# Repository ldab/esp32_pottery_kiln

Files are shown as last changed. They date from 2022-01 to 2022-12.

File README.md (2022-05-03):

# kiln_controller
Connected electric kiln controller -> esp32, max31855, thermocouple type K, relay, contactor and energy meter. Including Kiln built plans.







 ## TODO

- [ ] Temperature Ramp rate monitor;
- [ ] Cooling monitor;
- [ ] Cool upload progress: https://codepen.io/takaneichinose/pen/jOWXBBd

## VOID

"Lorem ipsum dolor sit amet, consectetur adipiscing elit, sed do eiusmod tempor incididunt ut labore et dolore magna aliqua. Ut enim ad minim veniam, quis nostrud exercitation ullamco laboris nisi ut aliquip ex ea commodo consequat. Duis aute irure dolor in reprehenderit in voluptate velit esse cillum dolore eu fugiat nulla pariatur. Excepteur sint occaecat cupidatat non proident, sunt in culpa qui officia deserunt mollit anim id est laborum."

## Bil of materials

Description | Price
------------ | -------------
[4x Modules enclosure](https://www.amazon.de/gp/product/B07K5X5KZQ/ref=ppx_yo_dt_b_asin_title_o00_s00?ie=UTF8&psc=1) | €8.00
[Energy meter with S0 output](https://www.amazon.de/gp/product/B083H7NT2R/ref=ppx_yo_dt_b_asin_title_o00_s01?ie=UTF8&psc=1) | €13.00
[HDR-15 Power Supply](https://www.amazon.de/gp/product/B06XWQSJGW/ref=ppx_yo_dt_b_asin_title_o00_s00?ie=UTF8&psc=1) | €13.00
[12v/16A Relay](https://www.tme.eu/se/en/details/pi85012dc00ld/electromagnetic-relays-sets/relpol/pi85-012dc-00ld/) | €13.00
esp32 | €5.00
max31855 | €10.00
[Type-K thermocouple](https://www.keramik-kraft.com/en/Kiln-Building--Repair/Pyrometry/Thermocouple-Nickel-Typ-K/Thermocouple-Type-K-open-with-flange-l-12cm.html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) | €50.00
Cables, terminals, etc | €10.00

Total: **€120.00**

## Element calculations

### Element power

* This is determined by the power outlet, i.e `230Vac@16A` -> **3680W**

* Some [resources](https://knifedogs.com/threads/heat-treat-oven-how-to-design-and-calculate-the-heating-elements.21072/) indicate 0.6 - 1.3 W/cm2 of wall -> `Aw = (30.4 * 30.4 * 2) + (30.4 * 34.2 * 4) = 6,007.04 cm2` therefore Element should be between *3604W* and *7800W*.

* [KMT-614](https://skutt.com/products-page/ceramic-kilns/kmt-614/) and [Ecotop 20](https://www.rohde.eu/en/arts-and-crafts/products/toploaders/ecotop-series/ecotop-20) are both ~20L with 2300W element and rated to [Cone 6](https://www.ortonceramic.com/files/2676/File/orton-cone-chart-2016.pdf), aka ~1260°C

### Element size

Using Kanthal D - Other variants were hard to find, Kanthal D can be bought at [eveks.se](https://eveks.se/kategorier/461-kanthal-tr%C3%A5d-01-5mm-v%C3%A4rmekabel-14765-kanthal-d-motst%C3%A5ndstr%C3%A5d-1-100-meter-4066435006815.html)

* 1.6mm -> R = 0.67 Ohms/m
* L = ( 3680 / 16^2 ) / 0.67 = **~21.5m**

### Surface Load

* Accordingly to Kanthal [datasheet](./extras/Kanthal%20handbook.pdf), kiln application should have a Surface Load between 3-9 W/cm2:

`3680 / (2pi x 0.08 x 2150) = **3.4**W/cm2`

* [furnace handbook](./extras/file1359965681_U3423.pdf) page 7 indicates max 2.4W/cm2 @ 1100°C

### Coil Diameter

* In order to avoid deformation on horizontal coils, the coild diameter should stay below 10mm accordingly to:

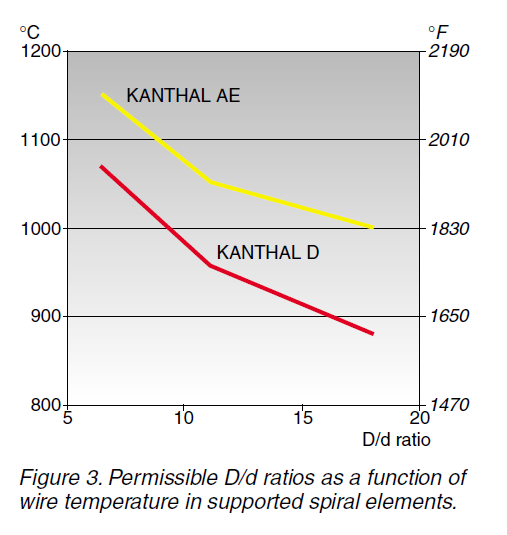
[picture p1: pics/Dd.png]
 

* Therefore let's use a **M8** rod to coil the wire.

### Coil Length

* The internal element perimeter is ~1216mm, if 3x turns are planned, we end up with a **3648mm** coil;

### Coil Pitch

*Coil pitch is normally 2-4 times the wire diameter* [page_79](./extras/Kanthal20handbook.pdf) -> aka 2-4mm

`s = (11.2 - 8) x pi / sqrt((21500 / 3648) ^ 2 - 1) = ~**2mm**`

## Bricks

The kils was build with [JM23](https://www.morganthermalceramics.com/media/4120/ifb-insulation-range-1100-1315-english.pdf) bricks

### Bricks thermal heat loss

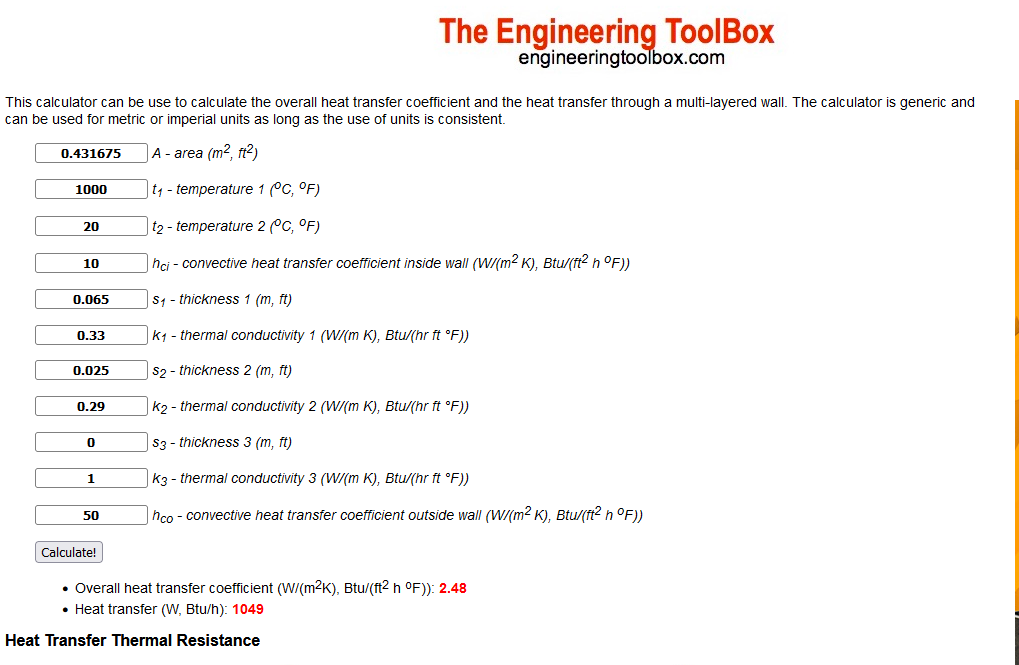
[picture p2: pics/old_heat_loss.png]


## PCB

PCB layout and files are found at [](./pcb/) open it with KiCad

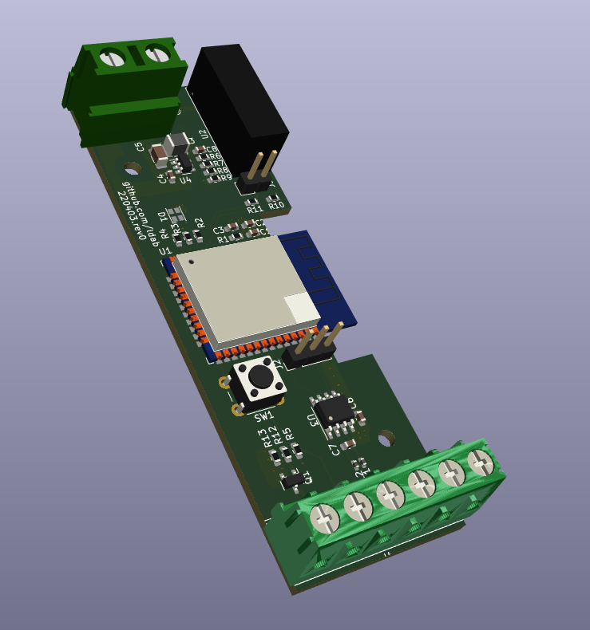
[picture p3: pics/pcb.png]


## Known Limitations

* 

## Credits

Github Shields and Badges created with [Shields.io](https://github.com/badges/shields/)

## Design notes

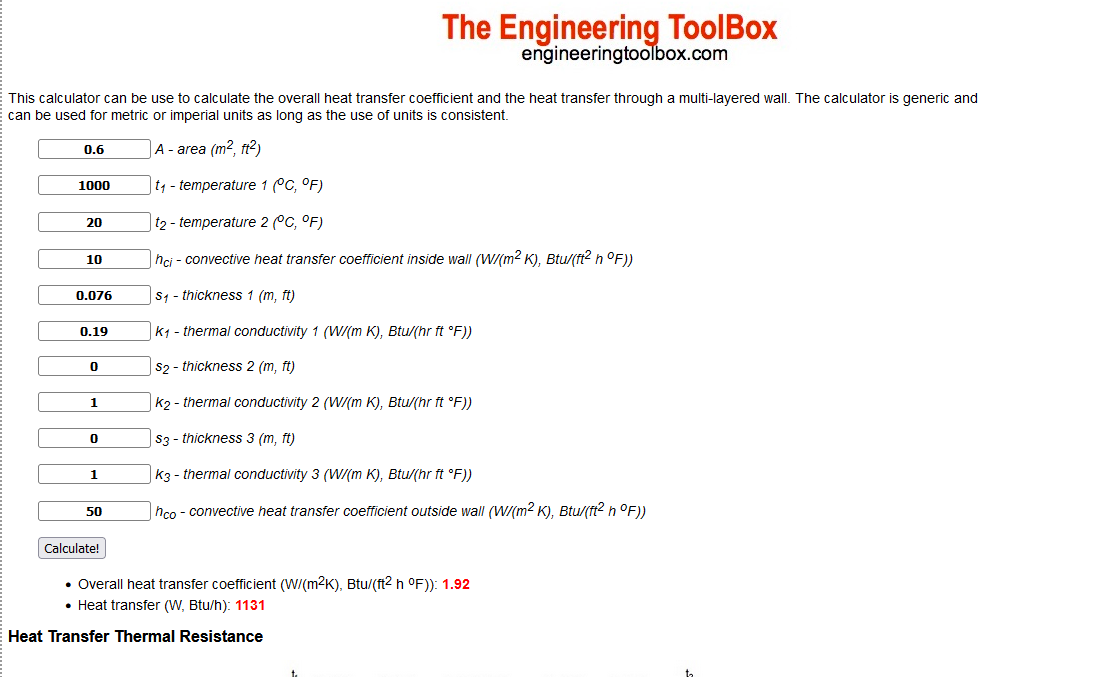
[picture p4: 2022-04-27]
pics/new_heat_loss.png

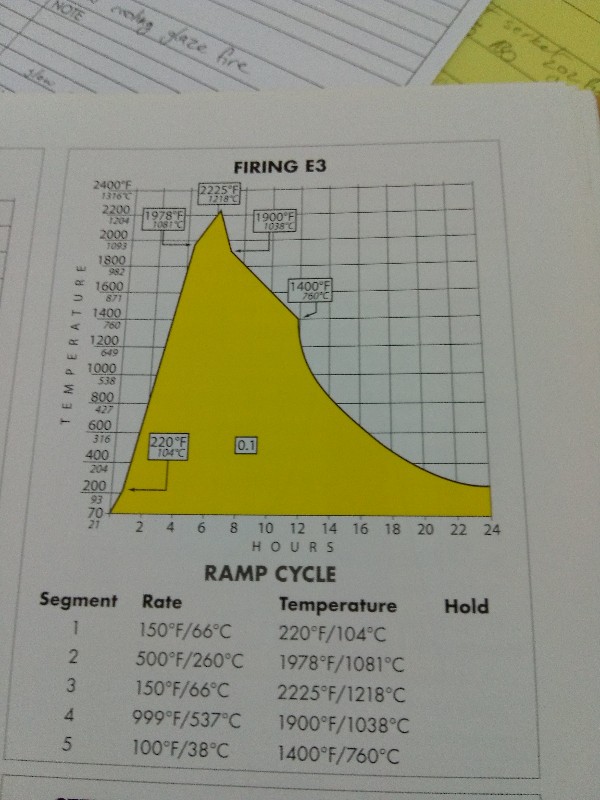
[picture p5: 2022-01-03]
extras/cone_ramp.jpg

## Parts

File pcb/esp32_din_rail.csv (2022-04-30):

Source: | C:\PERSONAL\kiln\pcb\esp32_din_rail.kicad_sch
Date: | 2022-04-26 16:50:59
Tool: | Eeschema (6.0.1)
Generator: | C:\Program Files\KiCad\6.0\bin\scripting\plugins/bom_csv_grouped_by_value.py
Component Count: | 38
Individual Components:
Item | Qty | Reference(s) | Value | LibPart | Footprint | Datasheet | LCSC | MANUFACTURER | Mouser | PARTREV | PN | STANDARD
 |  | C1 | 10u | Device:C_Small | Capacitor_SMD:C_0603_1608Metric | ~ |  |  |  |  | JMK107BJ106MA-T
 |  | C2 | 100n | Device:C_Small | Capacitor_SMD:C_0603_1608Metric | ~
 |  | C3 | 10u | Device:C_Small | Capacitor_SMD:C_0603_1608Metric | ~ |  |  |  |  | JMK107BJ106MA-T
 |  | C4 | 10u | Device:C_Small | Capacitor_SMD:C_0603_1608Metric | ~
 |  | C5 | 100u | Device:C_Small | Capacitor_SMD:C_1206_3216Metric | ~ | C77085
 |  | C6 | 100n | Device:C_Small | Capacitor_SMD:C_0603_1608Metric | ~
 |  | C7 | 100n | Device:C_Small | Capacitor_SMD:C_0603_1608Metric | ~
 |  | C8 | 100n | Device:C_Small | Capacitor_SMD:C_0603_1608Metric | ~
 |  | D1 | LED_RBAG | Device:LED_RBAG | LED_SMD:LED_Cree-PLCC4_2x2mm_CW | ~ | C108793
 |  | H1 | MountingHole | Mechanical:MountingHole | MountingHole:MountingHole_2.7mm_M2.5 | ~
 |  | H2 | MountingHole | Mechanical:MountingHole | MountingHole:MountingHole_2.7mm_M2.5 | ~
 |  | J1 | Screw_Terminal_01x02 | Connector:Screw_Terminal_01x02 | TerminalBlock_RND:TerminalBlock_RND_205-00067_1x02_P7.50mm_Horizontal | ~ |  |  | 691216910002
 |  | J2 | Conn_01x03 | Connector:Conn_01x03_Male | Connector_PinHeader_2.54mm:PinHeader_1x03_P2.54mm_Vertical | ~
 |  | J3 | DNP | Connector:Conn_01x02_Male | Connector_PinHeader_2.54mm:PinHeader_1x02_P2.54mm_Vertical | ~ |  |  |  |  | DNP
 |  | J4 | Screw_Terminal_01x06 | Connector:Screw_Terminal_01x06 | TerminalBlock_Phoenix:TerminalBlock_Phoenix_PT-1,5-6-5.0-H_1x06_P5.00mm_Horizontal | ~ |  |  | 1935200
 |  | JP1 | SolderJumper_2_Open | Jumper:SolderJumper_2_Open | Jumper:SolderJumper-2_P1.3mm_Open_RoundedPad1.0x1.5mm | ~
 |  | L1 | L_Small | Device:L_Small | Inductor_SMD:L_0402_1005Metric | ~ |  |  |  |  | BLM15HD102SN1D
 |  | L2 | L_Small | Device:L_Small | Inductor_SMD:L_0402_1005Metric | ~ |  |  |  |  | BLM15HD102SN1D
 |  | L3 | 4.7u | Device:L_Small | Inductor_SMD:L_1210_3225Metric | ~
 |  | Q1 | PMV60ENEAR | Transistor_FET:NTR2101P | Package_TO_SOT_SMD:SOT-23 | http://www.onsemi.com/pub/Collateral/NTR2101P-D.PDF |  |  | 771-PMV60ENEAR
 |  | R1 | 10K | Device:R_Small | Resistor_SMD:R_0603_1608Metric | ~
 |  | R2 | 1K | Device:R_Small | Resistor_SMD:R_0603_1608Metric | ~ | C384295
 |  | R3 | 1K | Device:R_Small | Resistor_SMD:R_0603_1608Metric | ~ | C384295
 |  | R4 | 1K | Device:R_Small | Resistor_SMD:R_0603_1608Metric | ~ | C384295
 |  | R5 | 1K | Device:R_Small | Resistor_SMD:R_0603_1608Metric | ~ | C384295
 |  | R6 | 10K | Device:R_Small | Resistor_SMD:R_0603_1608Metric | ~
 |  | R7 | 10K | Device:R_Small | Resistor_SMD:R_0603_1608Metric | ~
 |  | R8 | 10K | Device:R_Small | Resistor_SMD:R_0603_1608Metric | ~
 |  | R9 | 10K | Device:R_Small | Resistor_SMD:R_0603_1608Metric | ~
 |  | R10 | 10K | Device:R_Small | Resistor_SMD:R_0603_1608Metric | ~ |  |  |  |  | DNP
 |  | R11 | 10K | Device:R_Small | Resistor_SMD:R_0603_1608Metric | ~ |  |  |  |  | DNP
 |  | R12 | 1K | Device:R_Small | Resistor_SMD:R_0603_1608Metric | ~ | C384295
 |  | R13 | 10K | Device:R_Small | Resistor_SMD:R_0603_1608Metric | ~
 |  | SW1 | SW_Push | Switch:SW_Push | Button_Switch_THT:SW_PUSH_6mm | ~
 |  | U1 | ESP32-WROOM-32 | RF_Module:ESP32-WROOM-32 | RF_Module:ESP32-WROOM-32 | https://www.espressif.com/sites/default/files/documentation/esp32-wroom-32_datasheet_en.pdf
 |  | U2 | PDM2-S12-S3-S | PDM2-S12-S3-S:PDM2-S12-S3-S | PDM2-S12-S3-S:CONV_PDM2-S12-S3-S |  |  | CUI INC |  | 1.03 |  | MANUFACTURER RECOMMENDATIONS
 |  | U3 | MAX31855KASA | Sensor_Temperature:MAX31855KASA | Package_SO:SOIC-8_3.9x4.9mm_P1.27mm | http://datasheets.maximintegrated.com/en/ds/MAX31855.pdf
 |  | U4 | AP62201WU-7 | Regulator_Switching:DIO6970 | Package_TO_SOT_SMD:SOT-23-6 | http://www.dioo.com/uploads/product/20190313/7a4d03690a9be004035eb1035a429f24.pdf
Collated Components:
Item | Qty | Reference(s) | Value | LibPart | Footprint | Datasheet | LCSC | MANUFACTURER | Mouser | PARTREV | PN | STANDARD
1 | 3 | C1, C3, C4 | 10u | Device:C_Small | Capacitor_SMD:C_0603_1608Metric | ~ |  |  |  |  | JMK107BJ106MA-T
2 | 4 | C2, C6, C7, C8 | 100n | Device:C_Small | Capacitor_SMD:C_0603_1608Metric | ~
3 | 1 | C5 | 100u | Device:C_Small | Capacitor_SMD:C_1206_3216Metric | ~ | C77085
4 | 1 | D1 | LED_RBAG | Device:LED_RBAG | LED_SMD:LED_Cree-PLCC4_2x2mm_CW | ~ | C108793
5 | 2 | H1, H2 | MountingHole | Mechanical:MountingHole | MountingHole:MountingHole_2.7mm_M2.5 | ~
6 | 1 | J1 | Screw_Terminal_01x02 | Connector:Screw_Terminal_01x02 | TerminalBlock_RND:TerminalBlock_RND_205-00067_1x02_P7.50mm_Horizontal | ~ |  |  | 691216910002
7 | 1 | J2 | Conn_01x03 | Connector:Conn_01x03_Male | Connector_PinHeader_2.54mm:PinHeader_1x03_P2.54mm_Vertical | ~
8 | 1 | J3 | DNP | Connector:Conn_01x02_Male | Connector_PinHeader_2.54mm:PinHeader_1x02_P2.54mm_Vertical | ~ |  |  |  |  | DNP
9 | 1 | J4 | Screw_Terminal_01x06 | Connector:Screw_Terminal_01x06 | TerminalBlock_Phoenix:TerminalBlock_Phoenix_PT-1,5-6-5.0-H_1x06_P5.00mm_Horizontal | ~ |  |  | 1935200
10 | 1 | JP1 | SolderJumper_2_Open | Jumper:SolderJumper_2_Open | Jumper:SolderJumper-2_P1.3mm_Open_RoundedPad1.0x1.5mm | ~
11 | 2 | L1, L2 | L_Small | Device:L_Small | Inductor_SMD:L_0402_1005Metric | ~ |  |  |  |  | BLM15HD102SN1D
12 | 1 | L3 | 4.7u | Device:L_Small | Inductor_SMD:L_1210_3225Metric | ~
13 | 1 | Q1 | PMV60ENEAR | Transistor_FET:NTR2101P | Package_TO_SOT_SMD:SOT-23 | http://www.onsemi.com/pub/Collateral/NTR2101P-D.PDF |  |  | 771-PMV60ENEAR
14 | 8 | R1, R6, R7, R8, R9, R10, R11, R13 | 10K | Device:R_Small | Resistor_SMD:R_0603_1608Metric | ~ |  |  |  |  | DNP
15 | 5 | R2, R3, R4, R5, R12 | 1K | Device:R_Small | Resistor_SMD:R_0603_1608Metric | ~ | C384295
16 | 1 | SW1 | SW_Push | Switch:SW_Push | Button_Switch_THT:SW_PUSH_6mm | ~
17 | 1 | U1 | ESP32-WROOM-32 | RF_Module:ESP32-WROOM-32 | RF_Module:ESP32-WROOM-32 | https://www.espressif.com/sites/default/files/documentation/esp32-wroom-32_datasheet_en.pdf
18 | 1 | U2 | PDM2-S12-S3-S | PDM2-S12-S3-S:PDM2-S12-S3-S | PDM2-S12-S3-S:CONV_PDM2-S12-S3-S |  |  | CUI INC |  | 1.03 |  | MANUFACTURER RECOMMENDATIONS
19 | 1 | U3 | MAX31855KASA | Sensor_Temperature:MAX31855KASA | Package_SO:SOIC-8_3.9x4.9mm_P1.27mm | http://datasheets.maximintegrated.com/en/ds/MAX31855.pdf
20 | 1 | U4 | AP62201WU-7 | Regulator_Switching:DIO6970 | Package_TO_SOT_SMD:SOT-23-6 | http://www.dioo.com/uploads/product/20190313/7a4d03690a9be004035eb1035a429f24.pdf

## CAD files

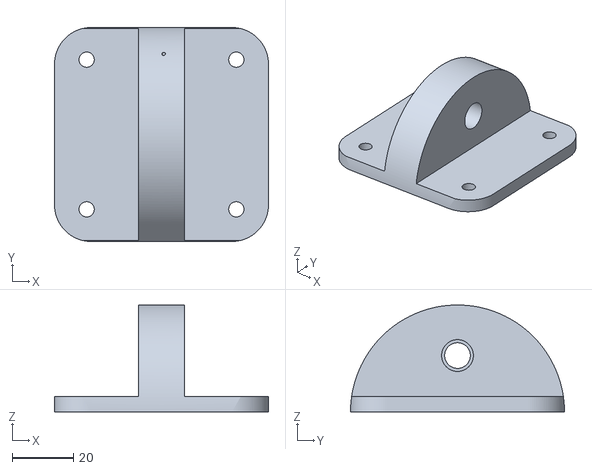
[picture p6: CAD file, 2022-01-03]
3D parts/coil_jig.stl
70.0 x 70.0 x 35.0

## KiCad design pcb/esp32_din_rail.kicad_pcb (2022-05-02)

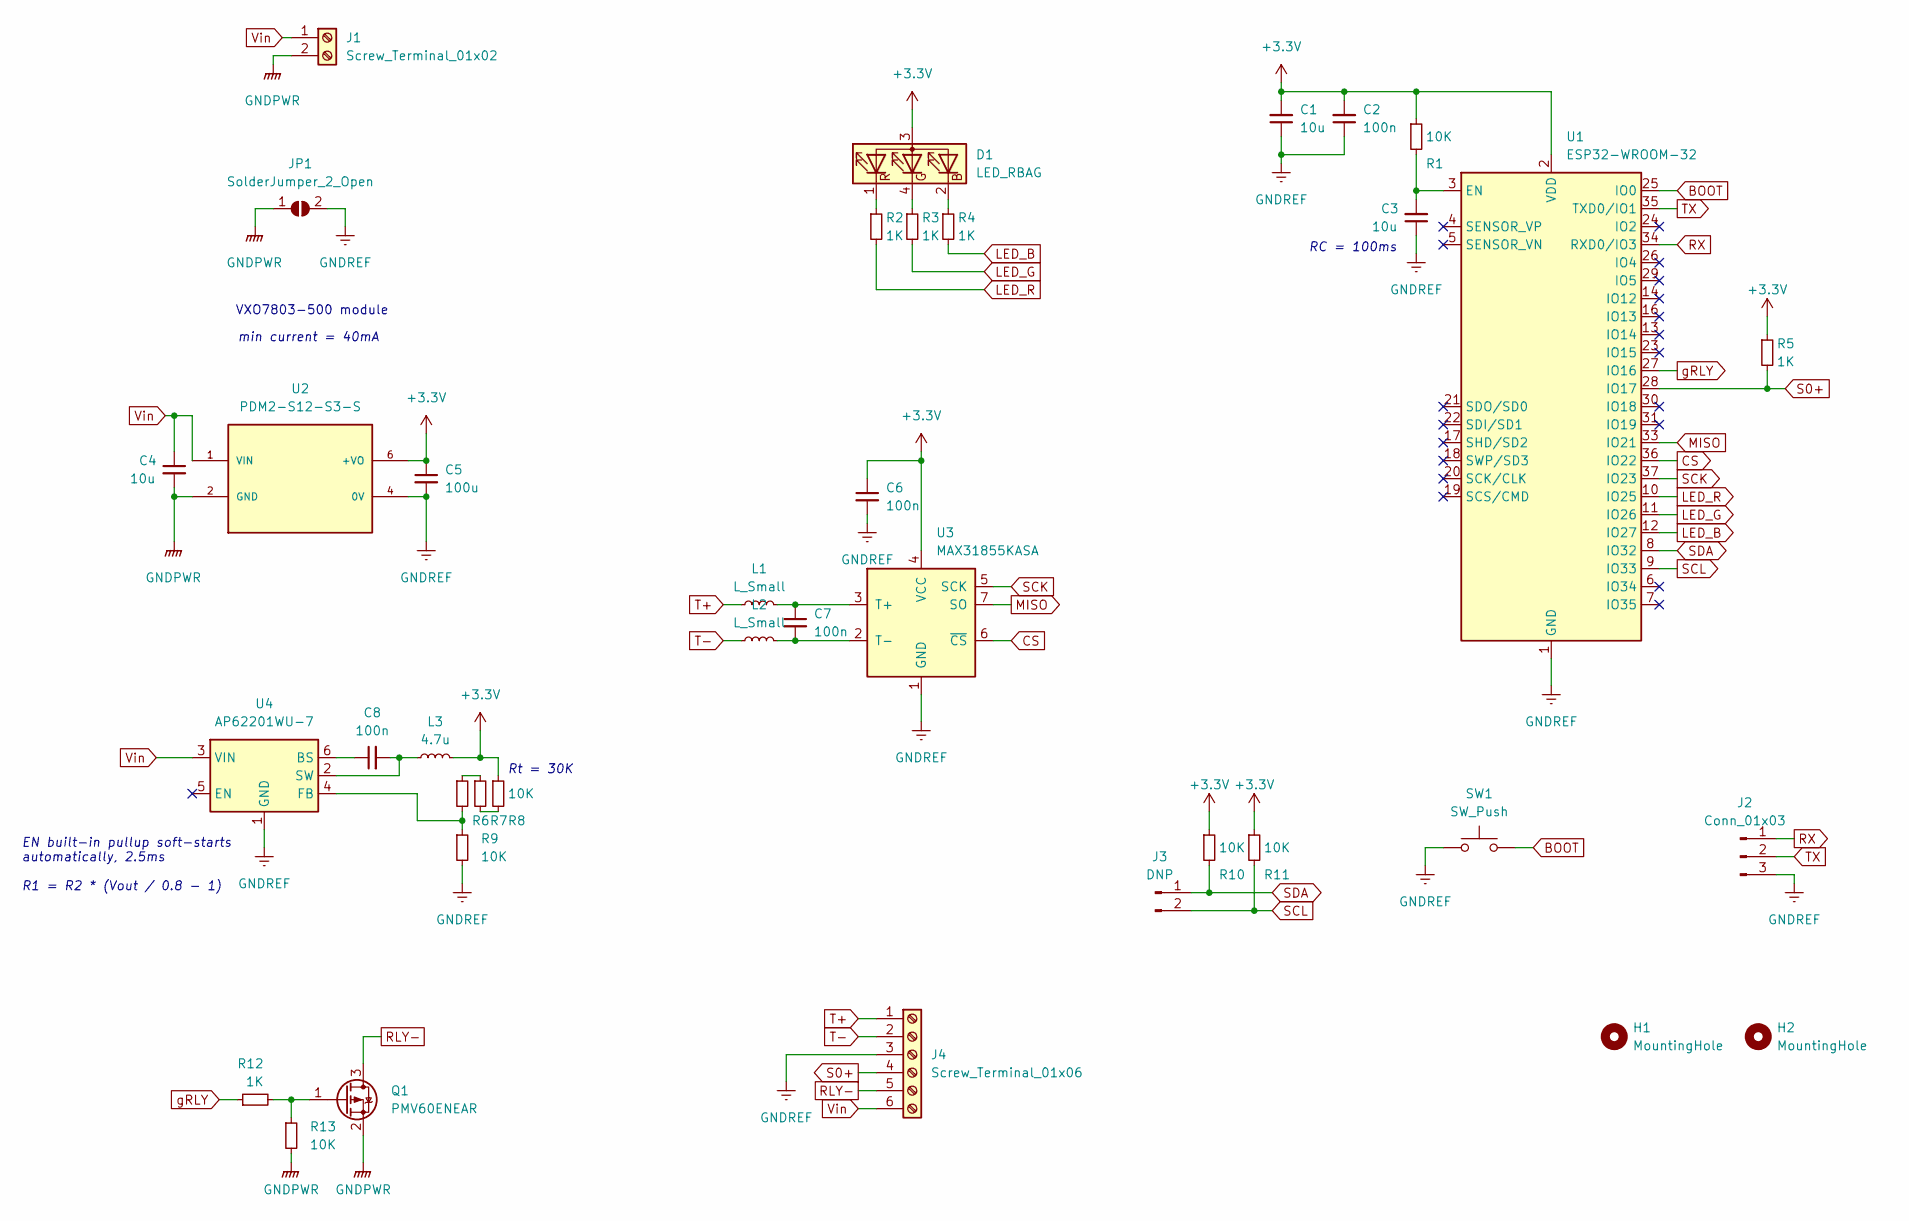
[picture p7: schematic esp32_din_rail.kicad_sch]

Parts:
C1, C3, C4: 10u; C_0603_1608Metric
C2, C6, C7, C8: 100n; C_0603_1608Metric
C5: 100u; C_1206_3216Metric; LCSC C77085
D1: LED_RBAG; LED_Cree-PLCC4_2x2mm_CW; LCSC C108793
H1, H2: MountingHole; MountingHole_2.7mm_M2.5
J1: Screw_Terminal_01x02; TerminalBlock_RND_205-00067_1x02_P7.50mm_Horizontal; Mouser 691216910002
J2: Conn_01x03; PinHeader_1x03_P2.54mm_Vertical
J3: DNP; PinHeader_1x02_P2.54mm_Vertical
J4: Screw_Terminal_01x06; TerminalBlock_Phoenix_PT-1,5-6-5.0-H_1x06_P5.00mm_Horizontal; Mouser 1935200
JP1: SolderJumper_2_Open; SolderJumper-2_P1.3mm_Open_RoundedPad1.0x1.5mm
L1, L2: L_Small; L_0402_1005Metric
L3: 4.7u; L_1210_3225Metric
Q1: PMV60ENEAR; SOT-23; Mouser 771-PMV60ENEAR
R1, R6, R7, R8, R9, R10, R11, R13: 10K; R_0603_1608Metric
R2, R3, R4, R5, R12: 1K; R_0603_1608Metric; LCSC C384295
SW1: SW_Push; SW_PUSH_6mm
U1: ESP32-WROOM-32
U2: PDM2-S12-S3-S; CONV_PDM2-S12-S3-S; PARTREV 1.03
U3: MAX31855KASA; SOIC-8_3.9x4.9mm_P1.27mm
U4: AP62201WU-7; SOT-23-6

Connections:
+3V3: C1.2, C2.2, C5.1, C6.1, D1.3 (A), L3.2, R1.1, R5.1, R8.1, R10.1, R11.1, U1.2 (VDD), U2.6 (+VO), U3.4 (VCC)
BOOT: SW1.2, U1.25 (IO0)
CS: U1.36 (IO22), U3.6 (~CS)
GNDPWR: C4.2, J1.2, JP1.1 (A), Q1.2 (S), R13.2, U2.2 (GND)
GNDREF: C1.1, C2.1, C3.1, C5.2, C6.2, J2.3, J4.3, JP1.2 (B), R9.2, SW1.1, U1.1 (GND), U1.15 (GND), U1.38 (GND), U1.39 (GND), U2.4 (0V), U3.1 (GND), U4.1 (GND)
LED_B: R4.2, U1.12 (IO27)
LED_G: R3.2, U1.11 (IO26)
LED_R: R2.2, U1.10 (IO25)
MISO: U1.33 (IO21), U3.7 (SO)
unnamed: C3.2, R1.2, U1.3 (EN)
unnamed: C7.1, L1.2, U3.3 (T+)
unnamed: C7.2, L2.2, U3.2 (T-)
unnamed: C8.1, U4.6 (BS)
unnamed: C8.2, L3.1, U4.2 (SW)
unnamed: D1.1 (RK), R2.1
unnamed: D1.2 (BK), R4.1
unnamed: D1.4 (GK), R3.1
unnamed: Q1.1 (G), R12.2, R13.1
unnamed: R6.1, R7.1
unnamed: R6.2, R9.1, U4.4 (FB)
unnamed: R7.2, R8.2
RLY-: J4.5, Q1.3 (D)
RX: J2.1, U1.34 (RXD0/IO3)
S0+: J4.4, R5.2, U1.28 (IO17)
SCK: U1.37 (IO23), U3.5 (SCK)
SCL: J3.2, R11.2, U1.9 (IO33)
SDA: J3.1, R10.2, U1.8 (IO32)
T+: J4.1, L1.1
T-: J4.2, L2.1
TX: J2.2, U1.35 (TXD0/IO1)
Vin: C4.1, J1.1, J4.6, U2.1 (VIN), U4.3 (VIN)
gRLY: R12.1, U1.27 (IO16)

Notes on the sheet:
Rt = 30K
VXO7803-500 module
RC = 100ms
EN built-in pullup soft-starts automatically, 2.5ms R1 = R2 * (Vout / 0.8 - 1)
min current = 40mA

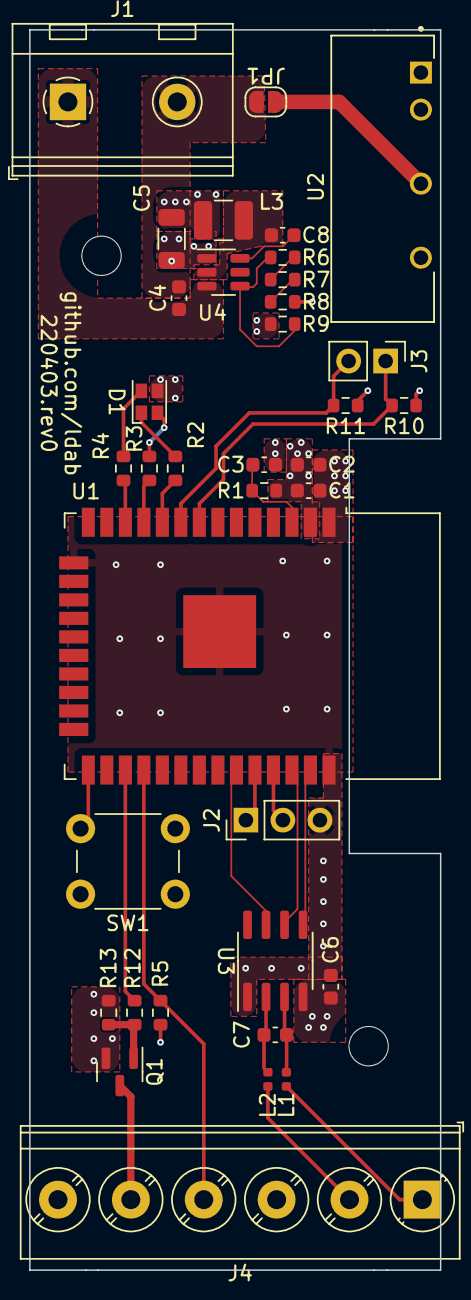
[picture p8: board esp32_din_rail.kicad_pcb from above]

Board: 4 copper layers, 28.2 x 85.1 mm, 38 parts (0 on the bottom side), 32 nets.

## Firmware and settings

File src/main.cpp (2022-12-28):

/******************************************************************************
main.cpp
ESP8266 based Kiln controller, thermocouple type K, MAX31855
Leonardo Bispo
March, 2022
https://github.com/ldab/kiln
Distributed as-is; no warranty is given.
******************************************************************************/

#include "ArduinoJson.h"

extern "C" {
#include "freertos/FreeRTOS.h"
#include "freertos/timers.h"
}

#include "ArduinoOTA.h"
#include <Arduino.h>
#include <WiFi.h>

#include <AsyncMqttClient.h>

#include "esp_system.h"
#include <Ticker.h>
#include <pthread.h>

#include <DNSServer.h>
#include <ESPmDNS.h>

#include <AsyncTCP.h>
#include <ESPAsyncWebServer.h>
#include <Update.h>

#include <HTTPClient.h>
#include <WiFiClientSecure.h>

#include "SPIFFS.h"

// PapertrailLogger
#include "PapertrailLogger.h"
#include <WiFiUdp.h>

// MAX31855
#include <SPI.h>
#include <Wire.h>

#include "Adafruit_MAX31855.h"

#include "time.h"

#include "html_strings.h"

#define PAPERTRAIL_HOST "logs2.papertrailapp.com"
#define PAPERTRAIL_PORT 53139

#ifdef VERBOSE
#define DBG(msg, ...)                                                          \
  {                                                                            \
    Serial.printf("[%lu] " msg, millis(), ##__VA_ARGS__);                      \
    Serial.flush();                                                            \
  }
#else
#define DBG(...)
#endif

#define NOTIFY(msg, ...)                                                       \
  {                                                                            \
    char _msg[64] = "";                                                        \
    sprintf(_msg, msg, ##__VA_ARGS__);                                         \
    Blynk.logEvent("alarm", _msg);                                             \
    DBG("%s\n", _msg);                                                         \
  }

// https://randomnerdtutorials.com/esp8266-pinout-reference-gpios/
#define RELAY        16
#define POWER        17
#define LED_R        25
#define LED_G        26
#define LED_B        27
#define SPI_CS       22
#define SPI_MISO     21
#define SPI_CLK      23
#define I2C_SDA      32
#define I2C_SCL      33

// Heating Rate (°C/hr) during the last 100°C of Firing
#define SLOWFIRE     15
#define MEDIUMFIRE   60
#define FASTFIRE     150

#define COSTKWH      2.14

#define RATEUPDATE   60 // every 60 seconds

#define DIFFERENTIAL 5 // degC

const char *p_mqtt   = "/mqtt.txt";
char mqtt_user[64]   = {'\0'};
char mqtt_pass[64]   = {'\0'};
char mqtt_server[64] = {'\0'};
uint16_t mqtt_port   = 1883;

String ssid, pass;

float temp;
float tInt;
float currentSetpoint = -9999;
std::vector<float> readings;
std::vector<long> epocTime;
volatile float current;
volatile uint32_t instPower;
volatile uint32_t energy = 0;
volatile uint32_t pulseInterval;

// Control variables
volatile uint32_t energyMillis = 0;
uint32_t initMillis            = 0;
uint32_t holdMillis            = 0;
int step                       = 0;

String info                    = "Idle 💤";

// Timer instance numbers
Ticker controlTimer;
Ticker safetyTimer;
Ticker rampTimer;
Ticker slowCool;
Ticker tempTimer;
Ticker sendTimer;
Ticker restart;

DNSServer dnsServer;

AsyncWebServer server(80);
AsyncEventSource events("/events"); // event source (Server-Sent events)
AsyncWebSocket ws("/ws");           // access at ws://[esp ip]/ws

Adafruit_MAX31855 thermocouple(SPI_CLK, SPI_CS, SPI_MISO);

PapertrailLogger *errorLog;

AsyncMqttClient mqttClient;
TimerHandle_t mqttReconnectTimer;
TimerHandle_t wifiReconnectTimer;

void printSegments();
void rampRate();
void tControl();
void getTemp();
String processor(const String &var);
String readFile(fs::FS &fs, const char *path);
void writeFile(fs::FS &fs, const char *path, const char *message);

typedef enum {
  RED,
  GREEN,
  BLUE,
  YELLOW,
  WHITE,
  PURPLE,
  CYAN,
} led_color_t;

class CaptiveRequestHandler : public AsyncWebHandler
{
  public:
  CaptiveRequestHandler() {}
  virtual ~CaptiveRequestHandler() {}

  bool canHandle(AsyncWebServerRequest *request)
  {
    // request->addInterestingHeader("ANY");
    return true;
  }

  void handleRequest(AsyncWebServerRequest *request)
  {
    request->send_P(200, "text/html", HTTP_CONFIG, processor);
  }
};

void espRestart() { ESP.restart(); }

void ledOff()
{
  digitalWrite(LED_R, HIGH);
  digitalWrite(LED_G, HIGH);
  digitalWrite(LED_B, HIGH);
}

void led(led_color_t color)
{
  ledOff();
  switch (color) {
  case RED:
    digitalWrite(LED_R, LOW);
    break;
  case GREEN:
    digitalWrite(LED_G, LOW);
    break;
  case BLUE:
    digitalWrite(LED_B, LOW);
    break;
  case YELLOW:
    digitalWrite(LED_R, LOW);
    digitalWrite(LED_G, LOW);
    break;
  case WHITE:
    digitalWrite(LED_R, LOW);
    digitalWrite(LED_G, LOW);
    digitalWrite(LED_B, LOW);
    break;
  case PURPLE:
    digitalWrite(LED_R, LOW);
    digitalWrite(LED_B, LOW);
    break;
  case CYAN:
    digitalWrite(LED_G, LOW);
    digitalWrite(LED_B, LOW);
    break;

  default:
    break;
  }
}

// Send notification to HA, max 32 bytes
void notify(char *msg, size_t length)
{
  DBG("%s\n", msg);
  char topic[64] = {'\0'};
  sprintf(topic, "%s/f/notify", mqtt_user);
  mqttClient.publish(topic, 0, false, msg, length);
}

void onUpload(AsyncWebServerRequest *request, String filename, size_t index,
              uint8_t *data, size_t len, bool final)
{
  if (!index) {
    DBG("Update Start: %s\n", filename.c_str());
    if (!Update.begin(UPDATE_SIZE_UNKNOWN)) {
      Update.printError(Serial);
    }
  }
  DBG("Progress: %u of %u\r", Update.progress(), Update.size());
  if (!Update.hasError()) {
    if (Update.write(data, len) != len) {
      Update.printError(Serial);
    }
  }
  if (final) {
    if (Update.end(true)) {
      DBG("Update Success: %uB\n", index + len);
      request->redirect("/");
      restart.once_ms(1000, espRestart);
    } else {
      Update.printError(Serial);
    }
  }
}

void onRequest(AsyncWebServerRequest *request)
{
  // Handle Unknown Request
  request->send(404, "text/plain", "OUCH");
}

void onEvent(AsyncWebSocket *server, AsyncWebSocketClient *client,
             AwsEventType type, void *arg, uint8_t *data, size_t len)
{
  // Handle WebSocket event
}

String processor(const String &var)
{
  if (var == "CSS_TEMPLATE")
    return FPSTR(HTTP_STYLE);
  if (var == "INDEX_JS")
    return FPSTR(HTTP_JS);
  if (var == "HTML_HEAD_TITLE")
    return FPSTR(HTML_HEAD_TITLE);
  if (var == "HTML_INFO_BOX") {
    String ret = "";
    if (WiFi.isConnected()) {
      ret = "<strong> Connected</ strong> to ";
      ret += WiFi.SSID();
      ret += "<br><em><small> with IP ";
      ret += WiFi.localIP().toString();
      ret += "</small>";
    } else
      ret = "<strong> Not Connected</ strong>";
    return ret;
  }
  if (var == "HTML_CONFIG_SSID")
    return WiFi.SSID();
  if (var == "UPTIME") {
    String ret = String(millis() / 1000 / 60);
    ret += " min ";
    ret += String((millis() / 1000) % 60);
    ret += " sec";
    return ret;
  }
  if (var == "CHIP_ID") {
    String ret = String((uint32_t)ESP.getEfuseMac());
    return ret;
  }
  if (var == "FREE_HEAP") {
    String ret = String(ESP.getFreeHeap());
    ret += " bytes";
    return ret;
  }
  if (var == "SKETCH_INFO") {
    //%USED_BYTES% / &FLASH_SIZE&<br><progress value="%USED_BYTES%"
    // max="&FLASH_SIZE&">
    String ret = String(ESP.getSketchSize());
    ret += " / ";
    ret += String(ESP.getFlashChipSize());
    ret += "<br><progress value=\"";
    ret += String(ESP.getSketchSize());
    ret += "\" max=\"";
    ret += String(ESP.getFlashChipSize());
    ret += "\">";
    return ret;
  }
  if (var == "HOSTNAME")
    return String(WiFi.getHostname());
  if (var == "MY_MAC")
    return WiFi.macAddress();
  if (var == "MY_RSSI")
    return String(WiFi.RSSI());
  if (var == "FW_VER")
    return String(FIRMWARE_VERSION);
  if (var == "SDK_VER")
    return String(ESP_ARDUINO_VERSION_MAJOR) + "." +
           String(ESP_ARDUINO_VERSION_MINOR) + "." +
           String(ESP_ARDUINO_VERSION_PATCH);
  if (var == "ABOUT_DATE") {
    String ret = String(__DATE__) + " " + String(__TIME__);
    return ret;
  }
  if (var == "GRAPH_DATA" && readings.size()) {
    String graphString;
    graphString.reserve(readings.size() * 2);
    graphString = "[";
    for (size_t i = 0; i < readings.size() - 1; i++) {
      graphString += "[";
      graphString += String(epocTime[i]);
      graphString += ",";
      graphString += String(readings[i], 0);
      graphString += "]";
      graphString += ",";
    }
    graphString += "[";
    graphString += String(epocTime[readings.size() - 1]);
    graphString += ",";
    graphString += String(readings[readings.size() - 1], 0);
    graphString += "]";
    graphString += "]";
    return graphString;
  }

  return String();
}

void configServer()
{
  server.on("/config", HTTP_POST, [](AsyncWebServerRequest *request) {
    int params = request->params();
    StaticJsonDocument<192> doc;
    char output[192] = {'\0'};
    for (int i = 0; i < params; i++) {
      AsyncWebParameter *p = request->getParam(i);
      if (p->isPost()) {
        // HTTP POST ssid value
        if (p->name() == "ssid") {
          ssid = p->value().c_str();
          DBG("SSID set to: %s\n", ssid.c_str());
        }
        if (p->name() == "pass") {
          pass = p->value().c_str();
          DBG("Password set to: %s\n", pass.c_str());
        }
        if (p->name() == "server") {
          doc["s"] = p->value().c_str();
        }
        if (p->name() == "mqtt_pass") {
          doc["pass"] = p->value().c_str();
        }
        if (p->name() == "user") {
          doc["u"] = p->value().c_str();
        }
        if (p->name() == "port") {
          doc["port"] = p->value().c_str();
        }
      }
    }
    serializeJson(doc, output);
    DBG("%s\n", output);
    writeFile(SPIFFS, p_mqtt, output);

    WiFi.persistent(true);
    WiFi.begin(ssid.c_str(), pass.c_str());
    DBG("Connecting to WiFi ..");
    while (WiFi.status() != WL_CONNECTED) {
      Serial.print('.');
      delay(100);
    }
    DBG("Connected\n");
    restart.once_ms(1000, espRestart);
    request->redirect("http://" + WiFi.localIP().toString());
  });
}

// Read File from SPIFFS
String readFile(fs::FS &fs, const char *path)
{
  DBG("Reading file: %s\r\n", path);

  File file = fs.open(path);
  if (!file || file.isDirectory()) {
    DBG("- failed to open file for reading\n");
    return String();
  }

  String fileContent;
  while (file.available()) {
    fileContent = file.readStringUntil('\n');
    DBG("Read: %s\n", fileContent.c_str());
    break;
  }
  return fileContent;
}

// Write file to SPIFFS
void writeFile(fs::FS &fs, const char *path, const char *message)
{
  DBG("Writing file: %s\r\n", path);

  File file = fs.open(path, FILE_WRITE);
  if (!file) {
    DBG("- failed to open file for writing\n");
    return;
  }
  if (file.print(message)) {
    DBG("- file written\n");
  } else {
    DBG("- frite failed\n");
  }
}

// temperature, rate, hold/soak (min)
int segments[4][3]     = {{0, 0, 0}, {0, 0, 0}, {0, 0, 0}, {0, 0, 0}};
const char *p_segments = "/segments.txt";

void onFire(AsyncWebServerRequest *request)
{
  int params = request->params();

  for (int i = 0; i < params; i++) {
    AsyncWebParameter *p = request->getParam(i);
    if (p->isPost()) {
      if (p->name() == "s00")
        segments[0][0] = p->value().toInt();
      if (p->name() == "s01")
        segments[0][1] = p->value().toInt();
      if (p->name() == "s02")
        segments[0][2] = p->value().toInt();
      if (p->name() == "s10")
        segments[1][0] = p->value().toInt();
      if (p->name() == "s11")
        segments[1][1] = p->value().toInt();
      if (p->name() == "s12")
        segments[1][2] = p->value().toInt();
      if (p->name() == "s20")
        segments[2][0] = p->value().toInt();
      if (p->name() == "s21")
        segments[2][1] = p->value().toInt();
      if (p->name() == "s22")
        segments[2][2] = p->value().toInt();
      if (p->name() == "s30")
        segments[3][0] = p->value().toInt();
      if (p->name() == "s31")
        segments[3][1] = p->value().toInt();
      if (p->name() == "s32")
        segments[3][2] = p->value().toInt();
    }
  }

  for (size_t i = 0; i < sizeof(segments) / sizeof(segments[0]); i++) {
    for (size_t j = 0; j < sizeof(segments[0]) / (sizeof(int)) - 1; j++) {
      if (segments[i][j] == 0) {
        DBG("Check the settings, i: %u j: %u\n", i, j);
        return;
      }
    }
  }

  if (/*segments[3][0] < segments[2][0] ||*/ segments[2][0] < segments[1][0] ||
      segments[1][0] < segments[0][0]) {
    DBG("Invalid Target temperature");
    return;
  }

  StaticJsonDocument<384> doc;
  char output[384]   = {'\0'};

  JsonObject preheat = doc.createNestedObject("preheat");
  preheat["st"]      = segments[0][0];
  preheat["r"]       = segments[0][1];
  preheat["h"]       = segments[0][2];

  JsonObject step1   = doc.createNestedObject("step1");
  step1["st"]        = segments[1][0];
  step1["r"]         = segments[1][1];
  step1["h"]         = segments[1][2];

  JsonObject step2   = doc.createNestedObject("step2");
  step2["st"]        = segments[2][0];
  step2["r"]         = segments[2][1];
  step2["h"]         = segments[2][2];

  JsonObject final   = doc.createNestedObject("final");
  final["st"]        = segments[3][0];
  final["r"]         = segments[3][1];
  final["h"]         = segments[3][2];

  serializeJson(doc, output);
  writeFile(SPIFFS, p_segments, output);

  if (true) { // TODO check disable button
    initMillis = millis();
    int tTotal = (segments[0][0] - temp) / segments[0][1] * 60 + segments[0][2];
    tTotal += (segments[1][0] - segments[0][0]) * 60 / segments[1][1] +
              segments[1][2];
    tTotal += (segments[2][0] - segments[1][0]) * 60 / segments[2][1] +
              segments[2][2];
    tTotal += (segments[3][0] - segments[2][0]) * 60 / segments[3][1] +
              segments[3][2];

    DBG("tTotal %dmin\n", tTotal);

    info = "Firing 🔥 @" + String(segments[step][0]) + "°C";
    led(PURPLE);

    printSegments();
    rampRate();
    controlTimer.attach_ms(5530L, tControl);
    rampTimer.attach_ms(RATEUPDATE * 1000L, rampRate);
  } else {
    DBG("Button pressed, disable temp control\n");
    writeFile(SPIFFS, p_segments, "");
    restart.once_ms(1000, espRestart);
  }
}

void onFire(String input)
{
  StaticJsonDocument<384> doc;
  deserializeJson(doc, input);

  segments[0][0] = doc["preheat"]["st"];
  segments[0][1] = doc["preheat"]["r"];
  segments[0][2] = doc["preheat"]["h"];
  segments[1][0] = doc["step1"]["st"];
  segments[1][1] = doc["step1"]["r"];
  segments[1][2] = doc["step1"]["h"];
  segments[2][0] = doc["step2"]["st"];
  segments[2][1] = doc["step2"]["r"];
  segments[2][2] = doc["step2"]["h"];
  segments[3][0] = doc["final"]["st"];
  segments[3][1] = doc["final"]["r"];
  segments[3][2] = doc["final"]["h"];

  getTemp();

  // guess the step
  // TODO publish retain and account for hold
  if (temp > segments[3][0])
    step = 3;
  else if (temp > segments[2][0])
    step = 3;
  else if (temp > segments[1][0])
    step = 2;
  else if (temp > segments[0][0])
    step = 1;

  currentSetpoint = temp;

  info            = "Firing 🔥 @" + String(segments[step][0]) + "°C";

  printSegments();
  rampRate();
  controlTimer.attach_ms(5530L, tControl);
  rampTimer.attach_ms(RATEUPDATE * 1000L, rampRate);
}

void sendData()
{
  StaticJsonDocument<192> doc;
  char payload[192];

  current          = (instPower / 1000.0f) / 230.0f;

  JsonObject feeds = doc.createNestedObject("feeds");
  feeds["T"]       = temp;
  feeds["I"]       = current;
  feeds["P"]       = instPower / 1000.0f;
  feeds["E"]       = energy;
  feeds["$"]       = energy / 1000.0f * COSTKWH;
  feeds["Tint"]    = tInt;
  feeds["St"]      = currentSetpoint;
  feeds["Step"]    = step;
  feeds["RSSI"]    = WiFi.RSSI();

  serializeJson(doc, payload);

  char topic[64] = {'\0'};
  sprintf(topic, "%s/g/kiln/json", mqtt_user);

  mqttClient.publish(topic, 0, false, payload, strlen(payload));

  DBG("topic: %s\n", topic);
  DBG("Publish: %s\n", payload);

  current   = 0;
  instPower = 0;
}

void safetyCheck()
{
  static bool tIntError  = false;
  static bool noRlyError = false;

  // if (controlTimer.active()) {
  //   if (temp > (currentSetpoint + 10)) // TODO check differential
  //   {
  //     DBG("HIGH TEMPERATURE ALARM\n");
  //   } else if (temp < (currentSetpoint - 20)) {
  //     DBG("LOW TEMPERATURE ALARM\n");
  //   }
  // }

  if (tInt > 60) {
    if (!tIntError) {
      char tIntChar[32];
      sprintf(tIntChar, "High internal temp: %.1f°C", tInt);
      notify(tIntChar, strlen(tIntChar));
      tIntError = true;
    }
  } else {
    tIntError = false;
  }

  if (digitalRead(RELAY)) {
    if ((millis() - energyMillis) > 2000L) {
      if (!noRlyError) {
        notify((char *)"noRlyError", strlen("noRlyError"));
        noRlyError = true;
      }
    } else {
      noRlyError = true;
    }
  }
}

void printSegments()
{
  DBG("Firing ");
  for (size_t i = 0; i < sizeof(segments) / sizeof(segments[0]); i++) {
    Serial.print("{");
    for (size_t j = 0; j < sizeof(segments[0]) / (sizeof(int)); j++) {
      Serial.printf("%d,", segments[i][j]);
    }
    Serial.print("} ");
  }
  Serial.print("\n");
}

void IRAM_ATTR readPower()
{
  if (energy == 0) {
    // We don't know the time difference between pulse, reset
    // TODO get from cloud in case MCU reset
    energy       = 1;
    current      = 0;
    instPower    = 0;

    energyMillis = millis();
  } else {
    pulseInterval = millis() - energyMillis;

    if (pulseInterval < 100) { // 10*sqrt(2) Amps =~ 1106.8ms
      // DBG("DEBOUNCE");
      return;
    }

    energy++;                         // each pulse is 0,5Wh
    instPower = 7200 * pulseInterval; // 1Wh = 3600J calculate in mW avoid float

    energyMillis = millis();
  }

  volatile static bool problem = false;
  if (digitalRead(RELAY)) {
    if (problem == true) {
      // notify((char *)"shortError", strlen("shortError"));
    }
    problem = true;
  } else
    problem = false;
}

void getTemp()
{
  static float _t   = 0;
  static uint8_t _s = 0;
  static bool tErr  = false;

  temp              = thermocouple.readCelsius();
  tInt              = thermocouple.readInternal();
  uint8_t error     = thermocouple.readError();

  // average 5x samples
  _t += temp;
  _s++;
  if (_s == 4) {
    temp = (float)(_t / _s);
    _t   = 0;
    _s   = 0;
  }

  // Ignore SCG fault
  // https://forums.adafruit.com/viewtopic.php?f=31&t=169135#p827564
  if (error & 0b001) {
    if (!tErr) {
      temp = NAN;
      tErr = true;

      char tcError[24];
      sprintf(tcError, "Thermocouple error #%i", error);
      notify(tcError, strlen(tcError));

      digitalWrite(RELAY, LOW);
    }
  } else {
    static uint32_t log = millis();
    tErr                = false;
    char msg[8];
    sprintf(msg, "%.01f", temp);

    struct tm timeinfo;
    if (((millis() - log) > (60 * 1000) || readings.size() == 0) &&
        getLocalTime(&timeinfo)) {
      time_t epoc = mktime(&timeinfo);
      epocTime.push_back((long)epoc);
      readings.push_back(temp);
      DBG("strlen: %u\n", readings.size());
      log = millis();
    }

    char instPowerString[8];
    sprintf(instPowerString, "%.01f", instPower / 1000.0f);
    events.send(msg, "temperature");
    events.send(instPowerString, "KW");
    DBG("T: %sdegC P: %sW\n", msg, instPowerString);
  }
}

void holdTimer(uint32_t _segment)
{
  if (holdMillis == 0) {
    DBG("Start hold for %dmin\n", _segment);
    holdMillis = millis();
    rampTimer.detach();
  }
  uint32_t _elapsed = (millis() - holdMillis) / (60 * 1000);
  info = "Hold: " + String(currentSetpoint, 0) + "°C-" + String(_elapsed) +
         "/" + String(_segment) + "min";
  events.send(info.c_str(), "display");

  if (_elapsed >= _segment) {
    step++;
    holdMillis = 0;
    rampTimer.attach_ms(RATEUPDATE * 1000L, rampRate);
    DBG("Done with hold, step: %d\n", step);
    info = "Firing 🔥 @" + String(segments[step][0]) + "°C";
    events.send(info.c_str(), "display");
  }
}

void rampDown()
{
  // https://digitalfire.com/schedule/04dsdh
  if (currentSetpoint < 760 || step == 5) {
    controlTimer.detach();
    slowCool.detach();
    currentSetpoint = 0;
    tControl();
    writeFile(SPIFFS, p_segments, "");
    info = "Cooling ❄️";
    events.send(info.c_str(), "display");
  }

  currentSetpoint -= (float)(83.0 / (3600.0f / RATEUPDATE));
}
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
void loop()
{
  if (WiFi.getMode() == WIFI_MODE_AP || WiFi.getMode() == WIFI_MODE_APSTA)
    dnsServer.processNextRequest();

  // ArduinoOTA.handle();
}

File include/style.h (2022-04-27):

#include "Arduino.h"

const char HTTP_STYLE[] PROGMEM = R"rawliteral(
.c,
body {
  text-align: center;
  font-family: verdana
}

div,
input,
select {
  padding: 5px;
  font-size: 1em;
  margin: 5px 0;
  box-sizing: border-box
}

input,
button,
select,
.msg {
  border-radius: .3rem;
  width: 100%%
}

input[type=radio],
input[type=checkbox] {
  width: auto
}

button,
input[type='button'],
input[type='submit'] {
  cursor: pointer;
  border: 0;
  background-color: #1fa3ec;
  color: #fff;
  line-height: 2.4rem;
  font-size: 1.2rem;
  width: 100%%
}

input[type='file'] {
  border: 1px solid #1fa3ec
}

.wrap {
  text-align: left;
  display: inline-block;
  min-width: 360px;
  max-width: 500px
}

a {
  color: #000;
  font-weight: 700;
  text-decoration: none
}

a:hover {
  color: #1fa3ec;
  text-decoration: underline
}

.q {
  height: 16px;
  margin: 0;
  padding: 0 5px;
  text-align: right;
  min-width: 38px;
  float: right
}

.q.q-0:after {
  background-position-x: 0
}

.q.q-1:after {
  background-position-x: -16px
}

.q.q-2:after {
  background-position-x: -32px
}

.q.q-3:after {
  background-position-x: -48px
}

.q.q-4:after {
  background-position-x: -64px
}

.q.l:before {
  background-position-x: -80px;
  padding-right: 5px
}

.ql .q {
  float: left
}

.q:after,
.q:before {
  content: '';
  width: 16px;
  height: 16px;
  display: inline-block;
  background-repeat: no-repeat;
  background-position: 16px 0;
  background-image: url('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');
}

@media (-webkit-min-device-pixel-ratio: 2),
(min-resolution: 192dpi) {

  .q:before,
  .q:after {
    background-image: url('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');
    background-size: 95px 16px;
  }
}

.msg {
  padding: 20px;
  margin: 20px 0;
  border: 1px solid #eee;
  border-left-width: 5px;
  border-left-color: #777
}

.msg h4 {
  margin-top: 0;
  margin-bottom: 5px
}

.msg.P {
  border-left-color: #1fa3ec
}

.msg.P h4 {
  color: #1fa3ec
}

.msg.D {
  border-left-color: #dc3630
}

.msg.D h4 {
  color: #dc3630
}

.msg.S {
  border-left-color: #5cb85c
}

.msg.S h4 {
  color: #5cb85c
}

dt {
  font-weight: bold
}

dd {
  margin: 0;
  padding: 0 0 0.5em 0;
  min-height: 12px
}

td {
  vertical-align: top;
}

.h {
  display: none
}

button {
  transition: 0s opacity;
  transition-delay: 3s;
  transition-duration: 0s;
  cursor: pointer
}

button.D {
  background-color: #dc3630
}

button:active {
  opacity: 50%% !important;
  cursor: wait;
  transition-delay: 0s
}

body.invert,
body.invert a,
body.invert h1 {
  background-color: #060606;
  color: #fff;
}

body.invert .msg {
  color: #fff;
  background-color: #282828;
  border-top: 1px solid #555;
  border-right: 1px solid #555;
  border-bottom: 1px solid #555;
}

body.invert .q[role=img] {
  -webkit-filter: invert(1);
  filter: invert(1);
}

input:disabled {
  opacity: 0.5;
}

input,
button,
select,
.msg {
  border-radius: 0.3rem;
  width: 100%%;
}

.switch {
  position: relative;
  display: inline-block;
  width: 120px;
  height: 68px;
}

.switch input {
  display: none;
}

.slider {
  position: absolute;
  top: 0;
  left: 0;
  right: 0;
  bottom: 0;
  background-color: #ccc;
  border-radius: 6px;
}

.slider::before {
  position: absolute;
  content: "";
  height: 52px;
  width: 52px;
  left: 8px;
  bottom: 8px;
  background-color: #fff;
  -webkit-transition: 0.4s;
  transition: 0.4s;
  border-radius: 3px;
}

input:checked+.slider {
  background-color: #b30000;
}

input:checked+.slider::before {
  -webkit-transform: translateX(52px);
  -ms-transform: translateX(52px);
  transform: translateX(52px);
}
)rawliteral";

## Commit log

2022-01-03 Squashed commit of the following:
    commit eec104c16eb9b150623a43495655bbd0db684e37
    Author: ldab <l.bispo@live.com>
    Date: Sun Jan 2 20:43:48 2022 +0100
    temp differential
    commit 90ddbac9a1403a6511b5b3fb145a5e8f4b0a8779
    Author: ldab <l.bispo@live.com>
    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
    [min_ffat.csv]
2022-01-19 My pid
2022-01-20 include paperTrail
    [min_ffat.csv]
2022-03-13 Blynk 2.0 (#3)
    * stop sending variables as String
    * versioning and templateID
    * disable slow cooling
    * change notify
    * remove Time input and paperlog
    * wait currentST sync
2022-03-14 publish reset reason to papertrail (#4)
    * sync step from cloud
    * bump version / remove log
    * papertrail
    [main.cpp]
2022-03-17 fix crash but does not load from cloud, line 129
    faster sync
    [main.cpp]
2022-04-27 move to esp32 - dry run (#7)
    * import html
    * PCB
    * compatibility esp32
    * porting
    * mqtt
    * mqtt publish-work
    * fire param
    * include graph
    * /info page
    * plot real time
    * plot saved graph, crash at 100 readings
    * send data to graph, pthread
    * send graph data when page loads
    * fix surface load
    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
    [esp32_din_rail.kicad_pcb, esp32_din_rail.kicad_sch, partitions_custom.csv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]
2022-04-30 Arduino 200 (#8)
    * port arduino 2.0.0
    * reset button
    * fix time to load graph
    * led colors
    * fix interrupt, no float on ISR
    [esp32_din_rail.csv, esp32_din_rail.xls]
2022-05-02 fix wrong R5/R12 silk screen
    [esp32_din_rail.kicad_pcb]
2022-06-15 fix step recover after crash
    [main.cpp]

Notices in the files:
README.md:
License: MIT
